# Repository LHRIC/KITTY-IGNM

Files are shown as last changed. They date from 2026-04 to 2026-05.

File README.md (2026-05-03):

# 4-Cylinder Ignition Module PCB

This is a custom PCB ignition module for a 4-cylinder engine.

The board uses four IGBTs as low-side switches, with one IGBT for each ignition coil signal.

## What It Does

- Takes in 4 ignition signals
- Uses each signal to control one IGBT
- Each IGBT connects one coil to ground when active
- Designed for low-side ignition coil switching

## Power Distribution

The board also has a simple 12V splice section.

It takes:

- 2 × 12V inputs

And provides:

- 4 × 12V outputs

The 12V traces are only used to split power to the coils. They are not used anywhere else on the board.

## Notes

- Made for a 4-cylinder ignition setup
- Low-side switched design
- 12V section is only for coil power distribution
- Coil dwell/control timing should come from the ECU

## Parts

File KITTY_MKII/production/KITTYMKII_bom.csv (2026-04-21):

Designator | Footprint | Quantity | Value | LCSC Part #
C1 | 0805 | 1 | 33uF
C2 | 0603 | 1 | 1uF
C3 | 0603 | 1 | 100nF
D1, D2, D7, D8 | 0603 | 4 | LED
D3, D4, D5, D6 | D_SOD-523 | 4 | 10V
J1, J10, J11, J12, J13, J14, J15, J16, J2, J3, J4, J5, J6, J7, J8, J9 | SolderWire-1sqmm_1x01_D1.4mm_OD3.9mm | 16 | Conn_01x01_Pin
Q1, Q2, Q3, Q4 | TO-263-2 | 4 | Q_NIGBT_ECG
R1, R11, R12, R2 | 0603 | 4 | 10k
R10, R3, R4, R9 | 0603 | 4 | 680
R5, R6, R7, R8 | 0603 | 4 | 470
TP1, TP2, TP3, TP4, TP5, TP6 | TestPoint_Keystone_5000-5004_Miniature | 6 | TestPoint

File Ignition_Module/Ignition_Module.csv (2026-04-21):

Reference | Qty | Value | INV | Footprint
C1 | 1 | 33uF | LHR94 | Capacitor_SMD:C_0805_2012Metric_Pad1.18x1.45mm_HandSolder
C2 | 1 | 1uF | LHR18 | Capacitor_SMD:C_0603_1608Metric_Pad1.08x0.95mm_HandSolder
C3,C4,C5,C6 | 4 | 10nF | LHR14 | Capacitor_SMD:C_0603_1608Metric_Pad1.08x0.95mm_HandSolder
C7 | 1 | 100nF | LHR17 | Capacitor_SMD:C_0603_1608Metric_Pad1.08x0.95mm_HandSolder
D1,D5,D8,D11 | 4 | LED |  | LED_SMD:LED_0603_1608Metric_Pad1.05x0.95mm_HandSolder
D2,D3,D7,D10 | 4 | 10V |  | Diode_SMD:D_SOD-523
Q5,Q6,Q7,Q8 | 4 |  |  | IGBT
R1,R7,R12,R17 | 4 | 680 | LHR114 | Resistor_SMD:R_0603_1608Metric_Pad0.98x0.95mm_HandSolder
 | 8 | 47 | LHR1 | Resistor_SMD:R_0603_1608Metric_Pad0.98x0.95mm_HandSolder
R3,R8,R13,R18 | 4 | 10k | LHR8 | Resistor_SMD:R_0603_1608Metric_Pad0.98x0.95mm_HandSolder
R4,R5,R11,R16 | 4 | 470 | LHR34 | Resistor_SMD:R_0603_1608Metric_Pad0.98x0.95mm_HandSolder
TP1,TP2,TP3,TP4,TP5,TP6 | 6 | TestPoint |  | TestPoint:TestPoint_Keystone_5000-5004_Miniature

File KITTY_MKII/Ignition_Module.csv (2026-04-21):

Reference | Qty | Value | Footprint | Datasheet | INV
C1 | 1 | 33uF | Capacitor_SMD:C_0805_2012Metric_Pad1.18x1.45mm_HandSolder |  | LHR94
C2 | 1 | 1uF | Capacitor_SMD:C_0603_1608Metric_Pad1.08x0.95mm_HandSolder |  | LHR18
C7 | 1 | 100nF | Capacitor_SMD:C_0603_1608Metric_Pad1.08x0.95mm_HandSolder |  | LHR17
D1,D2,D7,D8 | 4 | LED | LED_SMD:LED_0603_1608Metric_Pad1.05x0.95mm_HandSolder
D3,D5,D10 | 3 | 10V | Diode_SMD:D_SOD-523
J1,J2,J3,J4,J5,J6,J7,J8,J9,J10,J11,J12,J13,J14,J15,J16 | 16 | Conn_01x01_Pin | Connector_Wire:SolderWire-1sqmm_1x01_D1.4mm_OD3.9mm
Q5,Q6,Q7,Q8 | 4 | Q_NIGBT_ECG | Package_TO_SOT_SMD:TO-263-2
R1,R8,R11,R12 | 4 | 10k,680 | Resistor_SMD:R_0603_1608Metric_Pad0.98x0.95mm_HandSolder |  | LHR114,LHR8
R3,R4,R17 | 3 | 680 | Resistor_SMD:R_0603_1608Metric_Pad0.98x0.95mm_HandSolder |  | LHR114
R5,R7,R8 | 3 | 470 | Resistor_SMD:R_0603_1608Metric_Pad0.98x0.95mm_HandSolder |  | LHR34
TP1,TP2,TP3,TP4,TP5,TP6 | 6 | TestPoint | TestPoint:TestPoint_Keystone_5000-5004_Miniature

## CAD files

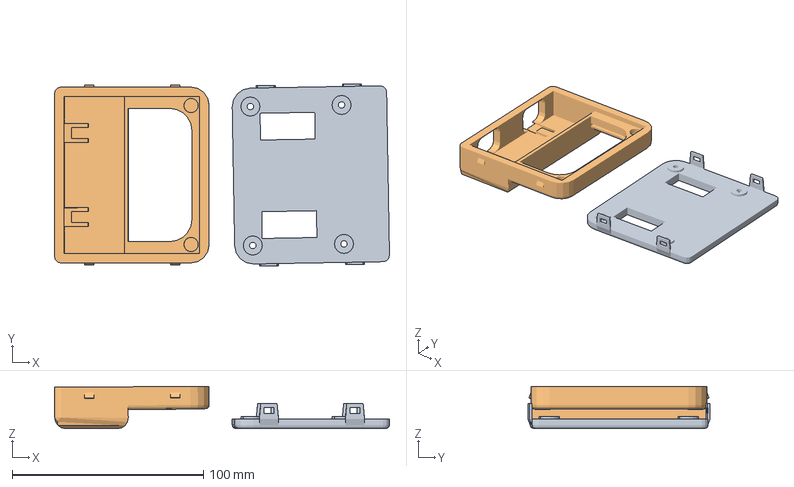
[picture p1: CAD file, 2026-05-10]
KITTY_MKII/enclosure_bottom2.3mf
175.2 x 95.3 x 22.2 mm
enclosure_bottom2.stl
enclosure_top2.stl

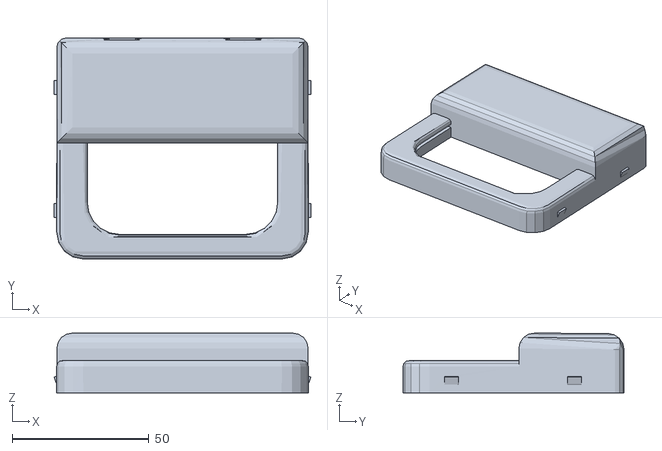
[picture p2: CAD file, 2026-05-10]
KITTY_MKII/enclosure_top2.stl
94.1 x 80.9 x 21.9

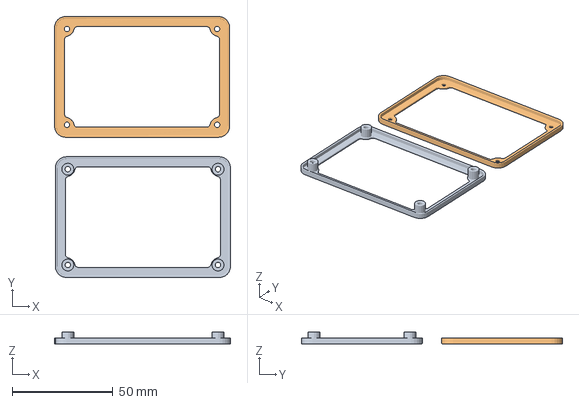
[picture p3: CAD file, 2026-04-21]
KITTY_MKII/enclosure_bottom.3mf
87.4 x 129.6 x 6.00 mm
enclosure_bottom.stl
enclosure_top.stl

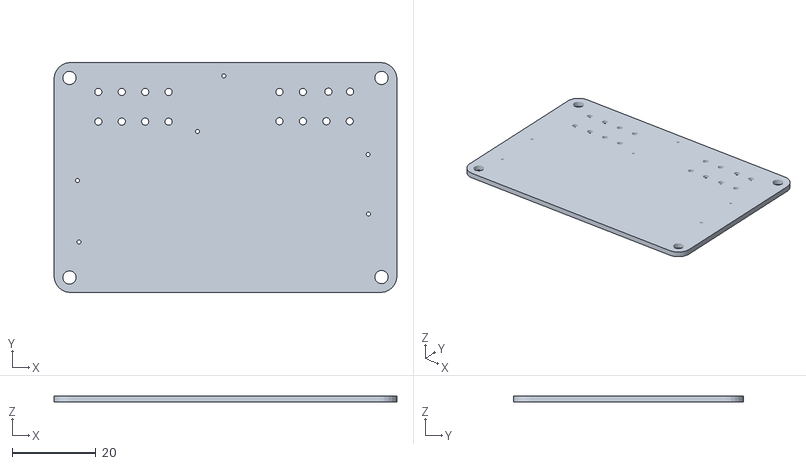
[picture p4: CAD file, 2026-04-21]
KITTY_MKII/pcb.stl
82.0 x 55.0 x 1.66

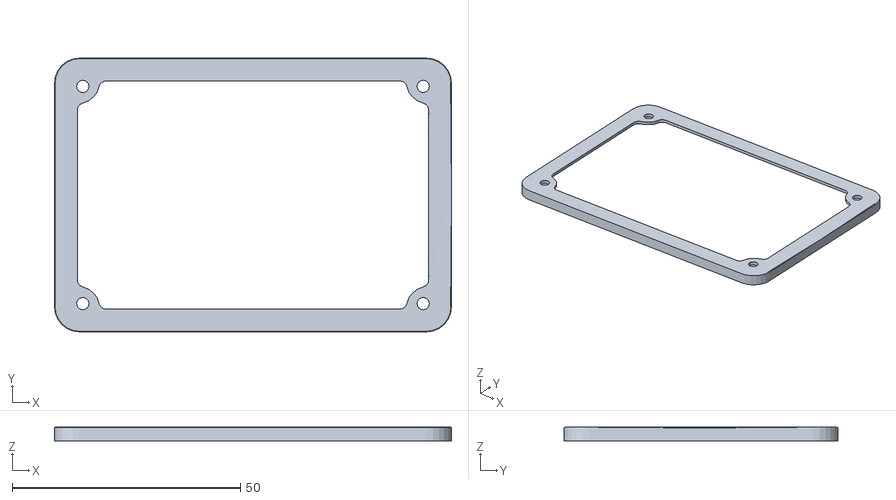
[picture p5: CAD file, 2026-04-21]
KITTY_MKII/enclosure_top.stl
87.0 x 60.0 x 2.99

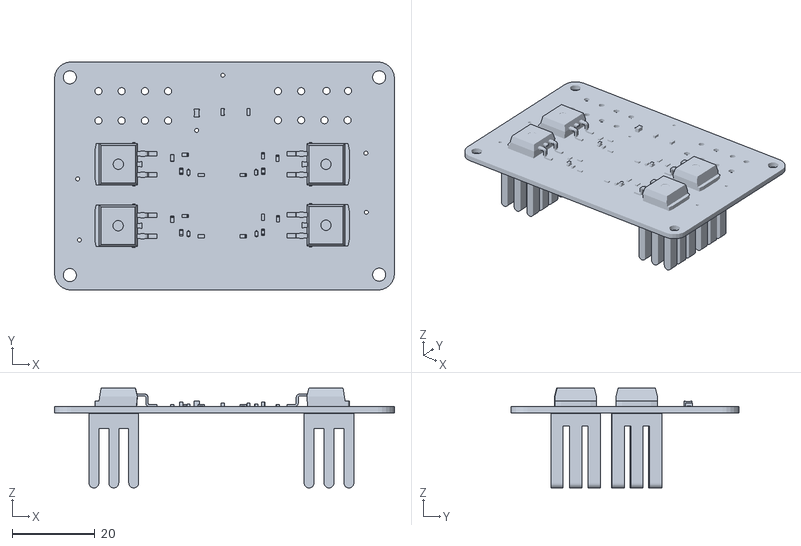
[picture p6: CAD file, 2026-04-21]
KITTY_MKII/KITTY.stl
82.0 x 55.0 x 24.1

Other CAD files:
KITTY_MKII/enclosure.blend
KITTY_MKII/enclosure_bottom.stl
KITTY_MKII/enclosure_bottom2.stl
KITTY_MKII/enclosure_rev2.blend

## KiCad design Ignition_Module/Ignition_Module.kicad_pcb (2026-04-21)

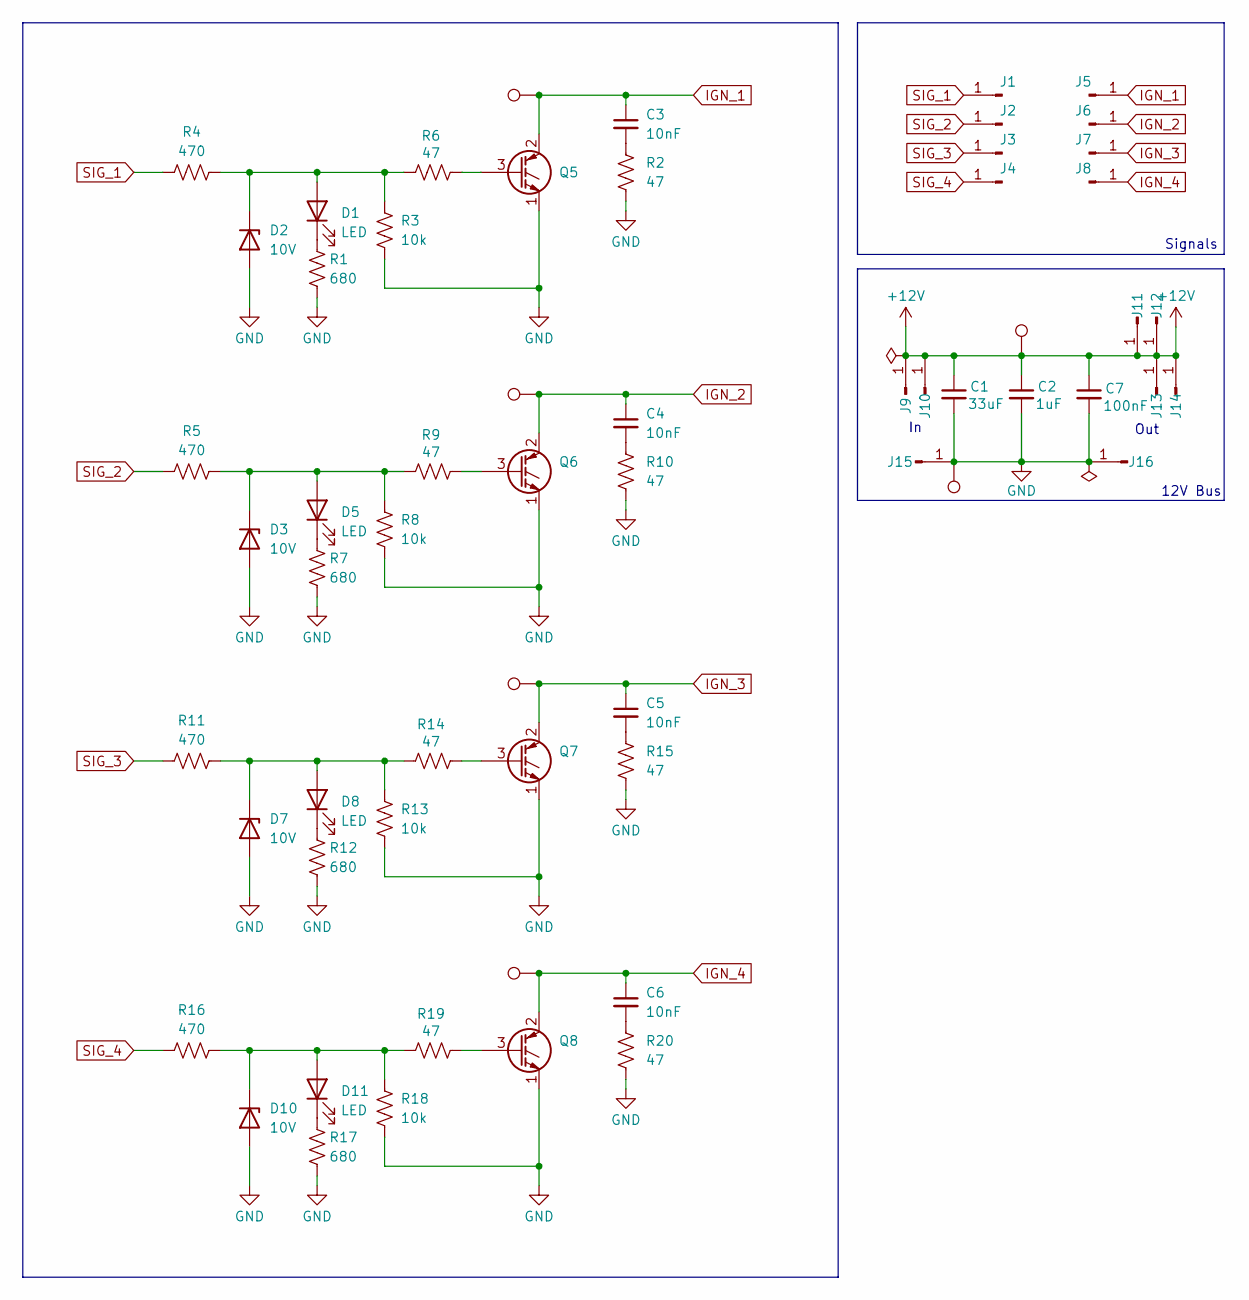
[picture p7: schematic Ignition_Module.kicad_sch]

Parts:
C1: 33uF; C_0805_2012Metric_Pad1.18x1.45mm_HandSolder
C2: 1uF; C_0603_1608Metric_Pad1.08x0.95mm_HandSolder
C3, C4, C5, C6: 10nF; C_0603_1608Metric_Pad1.08x0.95mm_HandSolder
C7: 100nF; C_0603_1608Metric_Pad1.08x0.95mm_HandSolder
D1, D5, D8, D11: LED; LED_0603_1608Metric_Pad1.05x0.95mm_HandSolder
D2, D3, D7, D10: 10V; D_SOD-523
J1, J2, J3, J4, J5, J6, J7, J8, J9, J10, J11, J12, J13, J14, J15, J16: Conn_01x01_Pin; SolderWire-1sqmm_1x01_D1.4mm_OD3.9mm
Q5, Q6, Q7, Q8: Q_NIGBT_ECG; TO-263-2
R1, R7, R12, R17: 680; R_0603_1608Metric_Pad0.98x0.95mm_HandSolder
R2, R6, R9, R10, R14, R15, R19, R20: 47; R_0603_1608Metric_Pad0.98x0.95mm_HandSolder
R3, R8, R13, R18: 10k; R_0603_1608Metric_Pad0.98x0.95mm_HandSolder
R4, R5, R11, R16: 470; R_0603_1608Metric_Pad0.98x0.95mm_HandSolder
TP1, TP2, TP3, TP4, TP5, TP6: TestPoint; TestPoint_Keystone_5000-5004_Miniature

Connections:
+12V: C1.1, C2.1, C7.1, J9.1, J10.1, J11.1, J12.1, J13.1, J14.1, TP2.1
GND: C1.2, C2.2, C7.2, D2.2 (A), D3.2 (A), D7.2 (A), D10.2 (A), J15.1, J16.1, Q5.1 (E), Q6.1 (E), Q7.1 (E), Q8.1 (E), R1.2, R2.2, R3.2, R7.2, R8.2, R10.2, R12.2, R13.2, R15.2, R17.2, R18.2, R20.2, TP1.1
IGN_1: C3.1, J5.1, Q5.2 (C), TP5.1
IGN_2: C4.1, J6.1, Q6.2 (C), TP4.1
IGN_3: C5.1, J7.1, Q7.2 (C), TP3.1
IGN_4: C6.1, J8.1, Q8.2 (C), TP6.1
unnamed: C3.2, R2.1
unnamed: C4.2, R10.1
unnamed: C5.2, R15.1
unnamed: C6.2, R20.1
unnamed: D1.2 (A), D2.1 (K), R3.1, R4.2, R6.1
unnamed: D1.1 (K), R1.1
unnamed: D3.1 (K), D5.2 (A), R5.2, R8.1, R9.1
unnamed: D5.1 (K), R7.1
unnamed: D7.1 (K), D8.2 (A), R11.2, R13.1, R14.1
unnamed: D8.1 (K), R12.1
unnamed: D10.1 (K), D11.2 (A), R16.2, R18.1, R19.1
unnamed: D11.1 (K), R17.1
unnamed: Q5.3 (G), R6.2
unnamed: Q6.3 (G), R9.2
unnamed: Q7.3 (G), R14.2
unnamed: Q8.3 (G), R19.2
SIG_1: J1.1, R4.1
SIG_2: J2.1, R5.1
SIG_3: J3.1, R11.1
SIG_4: J4.1, R16.1

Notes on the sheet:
Out
Signals
12V Bus

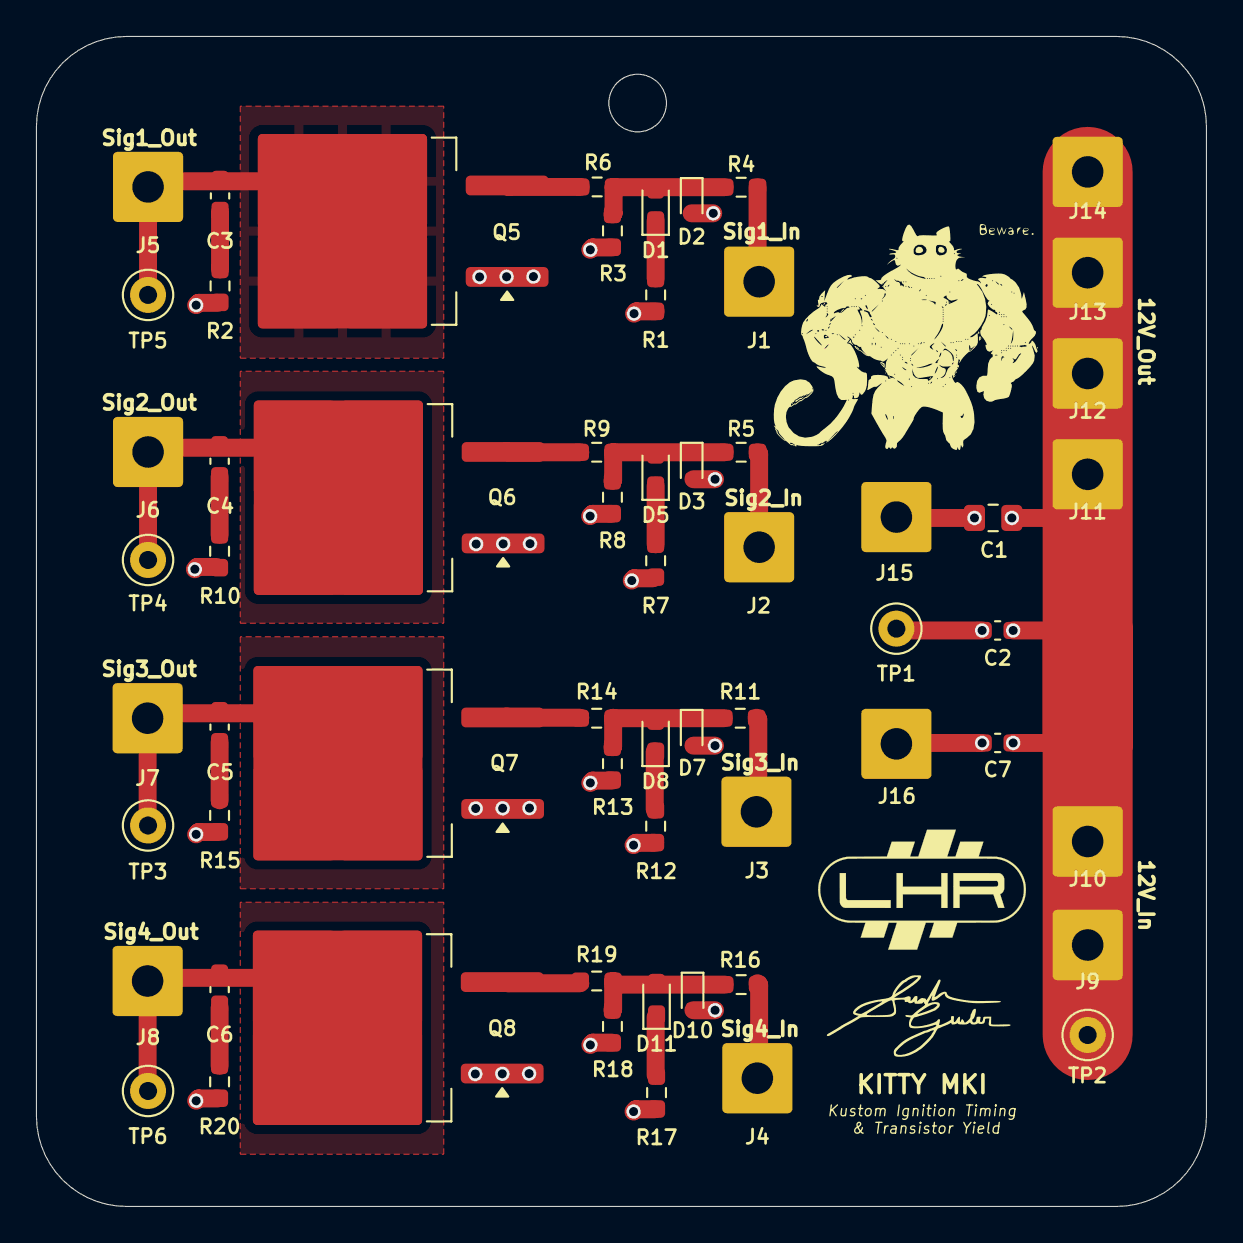
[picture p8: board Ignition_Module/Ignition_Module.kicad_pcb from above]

Board: 2 copper layers, 65.0 x 65.0 mm, 61 parts (0 on the bottom side), 26 nets.

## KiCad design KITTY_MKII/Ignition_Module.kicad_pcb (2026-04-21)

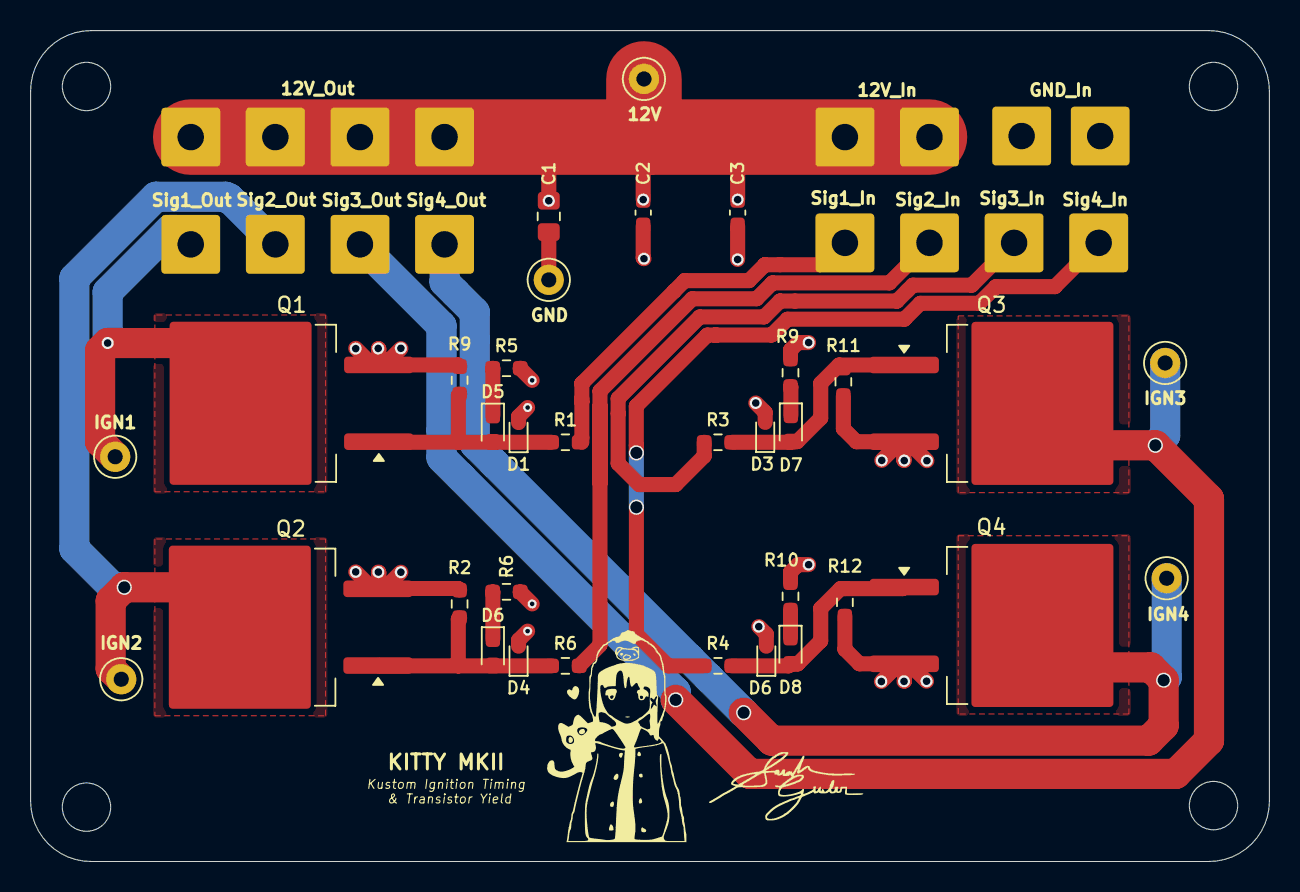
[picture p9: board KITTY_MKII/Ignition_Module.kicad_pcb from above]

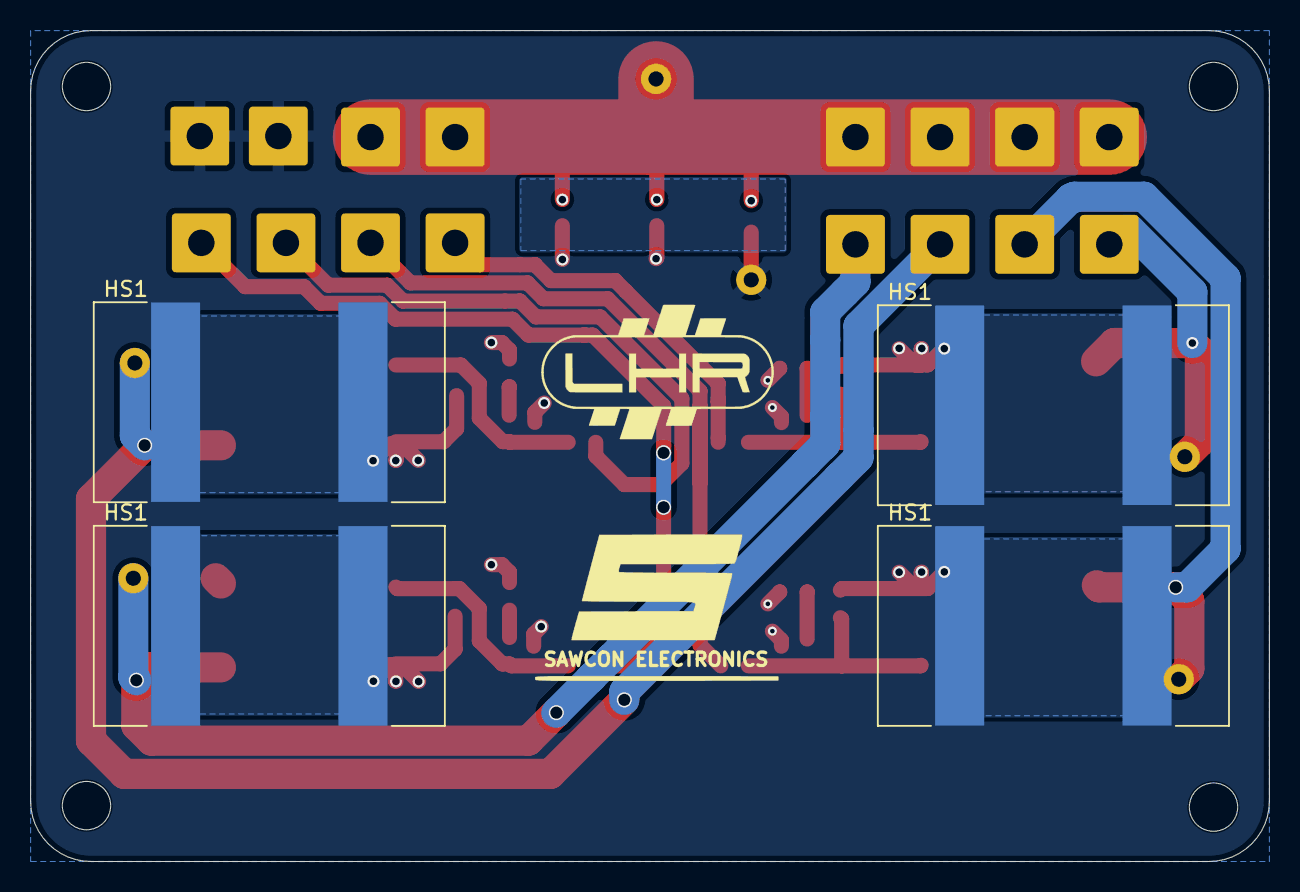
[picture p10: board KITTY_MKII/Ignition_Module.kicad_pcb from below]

Board: 2 copper layers, 82.0 x 55.0 mm, 53 parts (4 on the bottom side), 17 nets.

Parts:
C1: 33uF; C_0805_2012Metric_Pad1.18x1.45mm_HandSolder
C2: 1uF; C_0603_1608Metric_Pad1.08x0.95mm_HandSolder
C3: 100nF; C_0603_1608Metric_Pad1.08x0.95mm_HandSolder
D1, D3, D4, D6: 10V; D_SOD-523
D5, D6#2, D7, D8: LED; LED_0603_1608Metric_Pad1.05x0.95mm_HandSolder
HS1, HS1#2, HS1#3, HS1#4: Heatsink; Heatsink_Fischer_FK24413DPAK_23x13mm
J1, J2, J3, J4, J5, J6, J7, J8, J9, J10, J11, J12, J13, J14, J15, J16: Conn_01x01_Pin; SolderWire-1sqmm_1x01_D1.4mm_OD3.9mm
Q1, Q2, Q3, Q4: Q_NIGBT_ECG; TO-263-2
R1, R3, R4, R6: 470; R_0603_1608Metric_Pad0.98x0.95mm_HandSolder
R2, R9#2, R11, R12: 10k; R_0603_1608Metric_Pad0.98x0.95mm_HandSolder
R5, R6#2, R9, R10: 680; R_0603_1608Metric_Pad0.98x0.95mm_HandSolder
TP1, TP2, TP3, TP4, TP5, TP6: TestPoint; TestPoint_Keystone_5000-5004_Miniature

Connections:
+12V: C1.1, C2.1, C3.1, J1.1 (Pin_1_1), J3.1 (Pin_1_1), J13.1 (Pin_1_1), J14.1 (Pin_1_1), J15.1 (Pin_1_1), J16.1 (Pin_1_1), TP6.1 (1_1)
/Net-(D5-K): D6#2.1 (K), R6#2.1
/Net-(D7-K): D3.1 (K), D7.2 (A), R3.2, R11.1
GND: C1.2, C2.2, C3.2, D1.2 (A), D3.2 (A), D4.2 (A), D6.2 (A), J2.1 (Pin_1_1), J12.1 (Pin_1_1), Q1.3 (E), Q2.3 (E), Q3.3 (E), Q4.3 (E), R2.2, R5.2, R6#2.2, R9.2, R9#2.2, R10.2, R11.2, R12.2, TP5.1 (1_1)
IGN_1: J8.1 (Pin_1_1), Q1.2 (C), TP1.1 (1_1)
IGN_2: J9.1 (Pin_1_1), Q2.2 (C), TP2.1 (1_1)
IGN_3: J10.1 (Pin_1_1), Q3.2 (C), TP3.1 (1_1)
IGN_4: J11.1 (Pin_1_1), Q4.2 (C), TP4.1 (1_1)
unnamed: D1.1 (K), D5.2 (A), R1.2, R9#2.1
unnamed: D4.1 (K), Q2.1 (G), R2.1, R6.2
unnamed: D8.2 (A), R4.2, R12.1
unnamed: D5.1 (K), R5.1
unnamed: D6.1 (K), Q4.1 (G)
SIG_1: J4.1 (Pin_1_1), R1.1
SIG_2: J5.1 (Pin_1_1), R6.1
SIG_3: J6.1 (Pin_1_1), R3.1
SIG_4: J7.1 (Pin_1_1), R4.1

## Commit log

2026-02-13 all the stuff
    [Ignition_Module.kicad_pcb, Ignition_Module.kicad_sch]
2026-03-04 added mounting holes + silkscreen
    [Ignition_Module.kicad_pcb]
2026-03-04 removed diode - makes gate float 10V
    [Ignition_Module.kicad_pcb, Ignition_Module.kicad_sch]
2026-04-03 MKII, flipped footprint and rearranged.
    [Ignition_Module.csv, Ignition_Module.kicad_pcb, Ignition_Module.kicad_sch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]
2026-04-21 working on enclosure
    [Ignition_Module.csv, Ignition_Module.kicad_pcb, Ignition_Module.kicad_sch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]
2026-05-04 enclosure just needs latches/attachment points for the two halves
    [enclosure_rev2.blend]
2026-05-10 enclosure rev2 done, added latches
    [enclosure_bottom2.3mf, enclosure_bottom2.stl, enclosure_rev2.blend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]
